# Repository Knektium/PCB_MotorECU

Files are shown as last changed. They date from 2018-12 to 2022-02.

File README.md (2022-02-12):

Wolley Motor ECU
================

This is the KiCad project for the PCB that is used as ECU for the Wolley Wheel
and Fan modules.

It's a circular PCB that a brushed DC motor can be directly mounted on to be
controlled by the driver and MCU onboard through CAN.

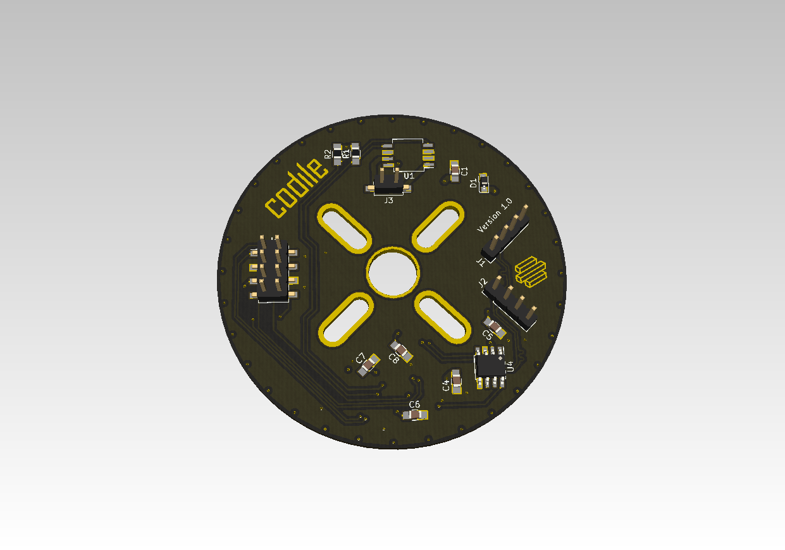
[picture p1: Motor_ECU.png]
PCB rendered in KiCad


Specifications
--------------

| Name | Value |
| --- | --- |
| PCB layers | 2 |
| PCB diameter | 61 mm |
| Max motor diameter | 28 mm |
| Motor center hole diameter | 10 mm |
| Motor voltage | 6 - 36 V |
| Max motor current | 6 A |
| Control Interface | CAN |

Key Components
--------------

| Component | Part | Details |
| --- | ---- | --- |
| MCU | Infineon XMC1404_F064X200A | ARM Cortex-M0, 32-bit, 48 MHz, 200 kB flash |
| Motor driver | Infineon IFX9201SG | 6 A and 36 V H-bridge with SPI diagnostics |
| CAN transceiver | Infineon TLE7251VSJ | |
| Speed sensor | Infineon TLE4964-4M | High precision unipolar hall effect switch |
| Temperature sensor | TI LM35DM | Precision centigrade temperature sensor |

Motor Alternatives
------------------

 - Mabuchi RS-385PV-2465
 - Mabuchi RS-365

Release Notes
-------------

Version 1.4:
 - Replaced the 4-pin connector with the new 5-pin connector.
 - Removed the battery power connector.

Version 1.3:
 - Moved the connectors closer to the middle to allow for more space and
   therefore better mounting.
 - Added a key hole to prevent the PCB from spinning when used as the
   CentrifugalFan ECU.
 - Joined the mount holes with the motor hole.
 - Smaller silk screen improvements.

Version 1.2 (same as CentrifugalFanECU v1.0):
 - Added a dedicated connector for the motor power.
 - Added a temperature sensor.
 - Added a status LED.
 - Removed two of the mount holes.
 - Made the motor hole bigger to fit a Mabuchi RS-380.

Version 1.1:
 - Replaced the motor driver with a better one that can handle up to 36 V.
 - Other improvements.

Licence
-------

Licenced under the CERN Open Hardware Licence v1.2.

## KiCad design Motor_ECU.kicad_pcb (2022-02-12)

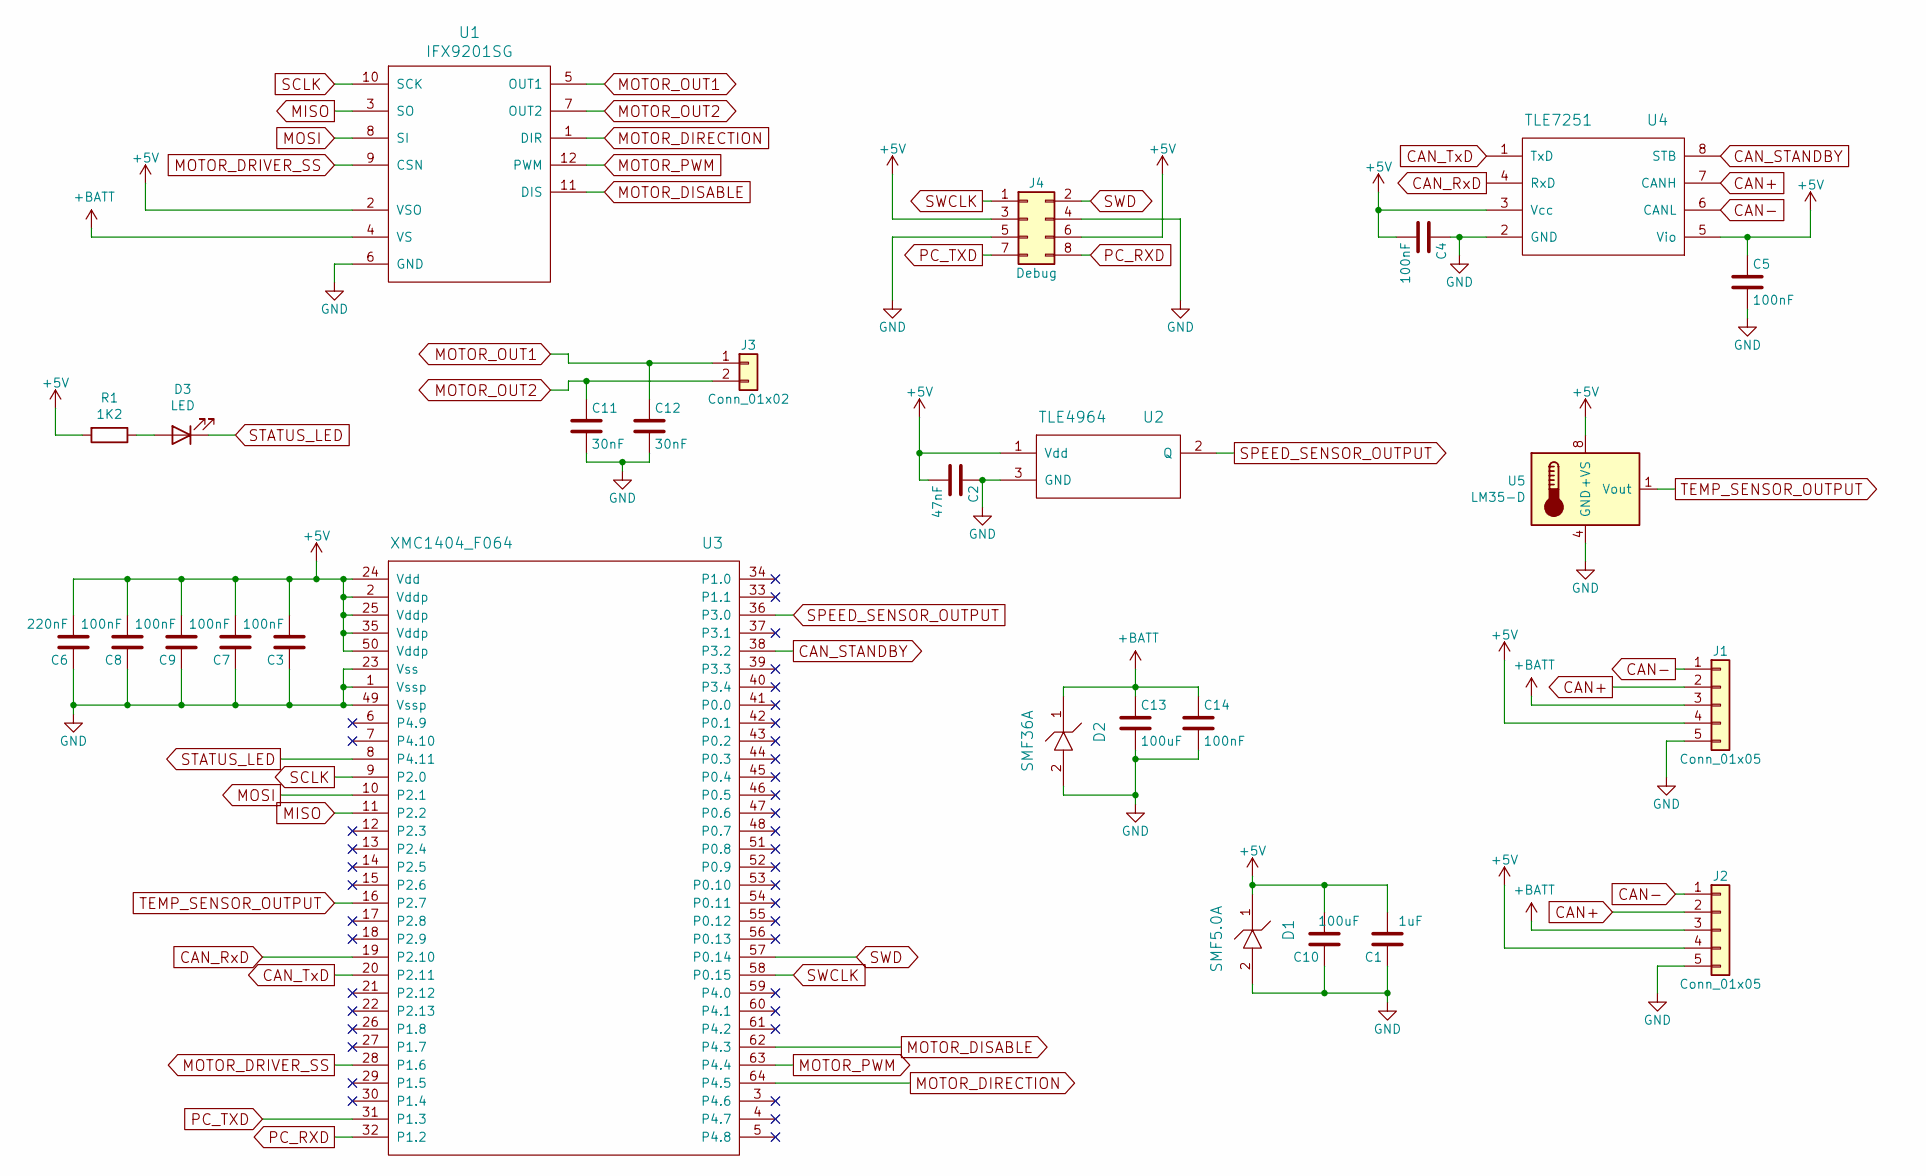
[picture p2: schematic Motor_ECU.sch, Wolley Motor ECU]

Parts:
C1: 1uF; C_0805_HandSoldering
C2: 47nF; C_0805_HandSoldering
C3, C4, C5, C7, C8, C9, C14: 100nF; C_0805_HandSoldering
C6: 220nF; C_0805_HandSoldering
C10, C13: 100uF; C_0805_HandSoldering
C11, C12: 30nF; C_0805_HandSoldering
D1: SMF5.0A; D_SOD-123F
D2: SMF36A; D_SOD-123F
D3: LED; C_0805_HandSoldering
J1, J2: Conn_01x05; PinHeader_1x05_P2.54mm_Vertical
J3: Conn_01x02; PinHeader_1x02_P2.54mm_Vertical
J4: Debug; Pin_Header_Straight_2x04_Pitch2.54mm_SMD
R1: 1K2; C_0805_HandSoldering
U1: IFX9201SG; SOIC-12_HeatSlugs
U2: TLE4964; TSOT-23_HandSoldering
U3: XMC1404_F064; TQFP-64_10x10mm_Pitch0.5mm_Handsoldering
U4: TLE7251; SOIC-8_3.9x4.9mm_Pitch1.27mm
U5: LM35-D; SOIC-8_3.9x4.9mm_P1.27mm

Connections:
+5V: C1.2, C2.2, C3.2, C4.2, C5.1, C6.2, C7.2, C8.2, C9.2, C10.2, D1.1, J1.4, J2.4, J4.3, J4.6, R1.2, U1.2 (VSO), U2.1 (Vdd), U3.2 (Vddp), U3.24 (Vdd), U3.25 (Vddp), U3.35 (Vddp), U3.50 (Vddp), U4.3 (Vcc), U4.5 (Vio), U5.8 (+VS)
+BATT: C13.1, C14.1, D2.1, J1.3, J2.3, U1.4 (VS)
CAN+: J1.2, J2.2, U4.7 (CANH)
CAN-: J1.1, J2.1, U4.6 (CANL)
CAN_RxD: U3.19 (P2.10), U4.4 (RxD)
CAN_STANDBY: U3.38 (P3.2), U4.8 (STB)
CAN_TxD: U3.20 (P2.11), U4.1 (TxD)
GND: C1.1, C2.1, C3.1, C4.1, C5.2, C6.1, C7.1, C8.1, C9.1, C10.1, C11.2, C12.2, C13.2, C14.2, D1.2, D2.2, J1.5, J2.5, J4.4, J4.5, U1.6 (GND), U2.3 (GND), U3.1 (Vssp), U3.23 (Vss), U3.49 (Vssp), U4.2 (GND), U5.4 (GND)
MISO: U1.3 (SO), U3.11 (P2.2)
MOSI: U1.8 (SI), U3.10 (P2.1)
MOTOR_DIRECTION: U1.1 (DIR), U3.64 (P4.5)
MOTOR_DISABLE: U1.11 (DIS), U3.62 (P4.3)
MOTOR_DRIVER_SS: U1.9 (CSN), U3.28 (P1.6)
MOTOR_OUT1: C12.1, J3.1, U1.5 (OUT1)
MOTOR_OUT2: C11.1, J3.2, U1.7 (OUT2)
MOTOR_PWM: U1.12 (PWM), U3.63 (P4.4)
unnamed: D3.2 (A), R1.1
PC_RXD: J4.8, U3.32 (P1.2)
PC_TXD: J4.7, U3.31 (P1.3)
SCLK: U1.10 (SCK), U3.9 (P2.0)
SPEED_SENSOR_OUTPUT: U2.2 (Q), U3.36 (P3.0)
STATUS_LED: D3.1 (K), U3.8 (P4.11)
SWCLK: J4.1, U3.58 (P0.15)
SWD: J4.2, U3.57 (P0.14)
TEMP_SENSOR_OUTPUT: U3.16 (P2.7), U5.1 (Vout)

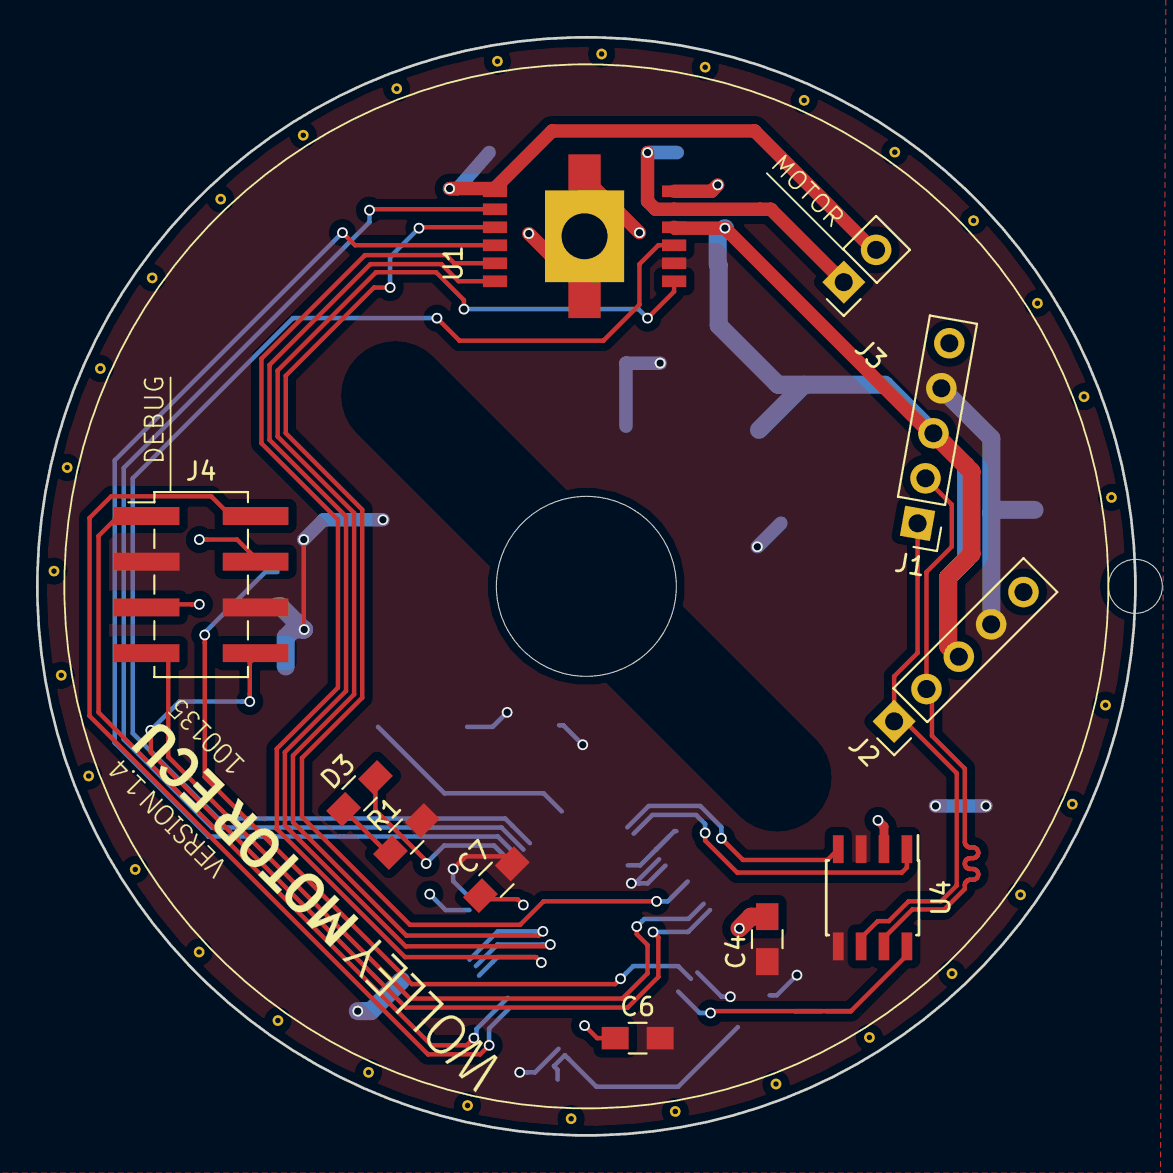
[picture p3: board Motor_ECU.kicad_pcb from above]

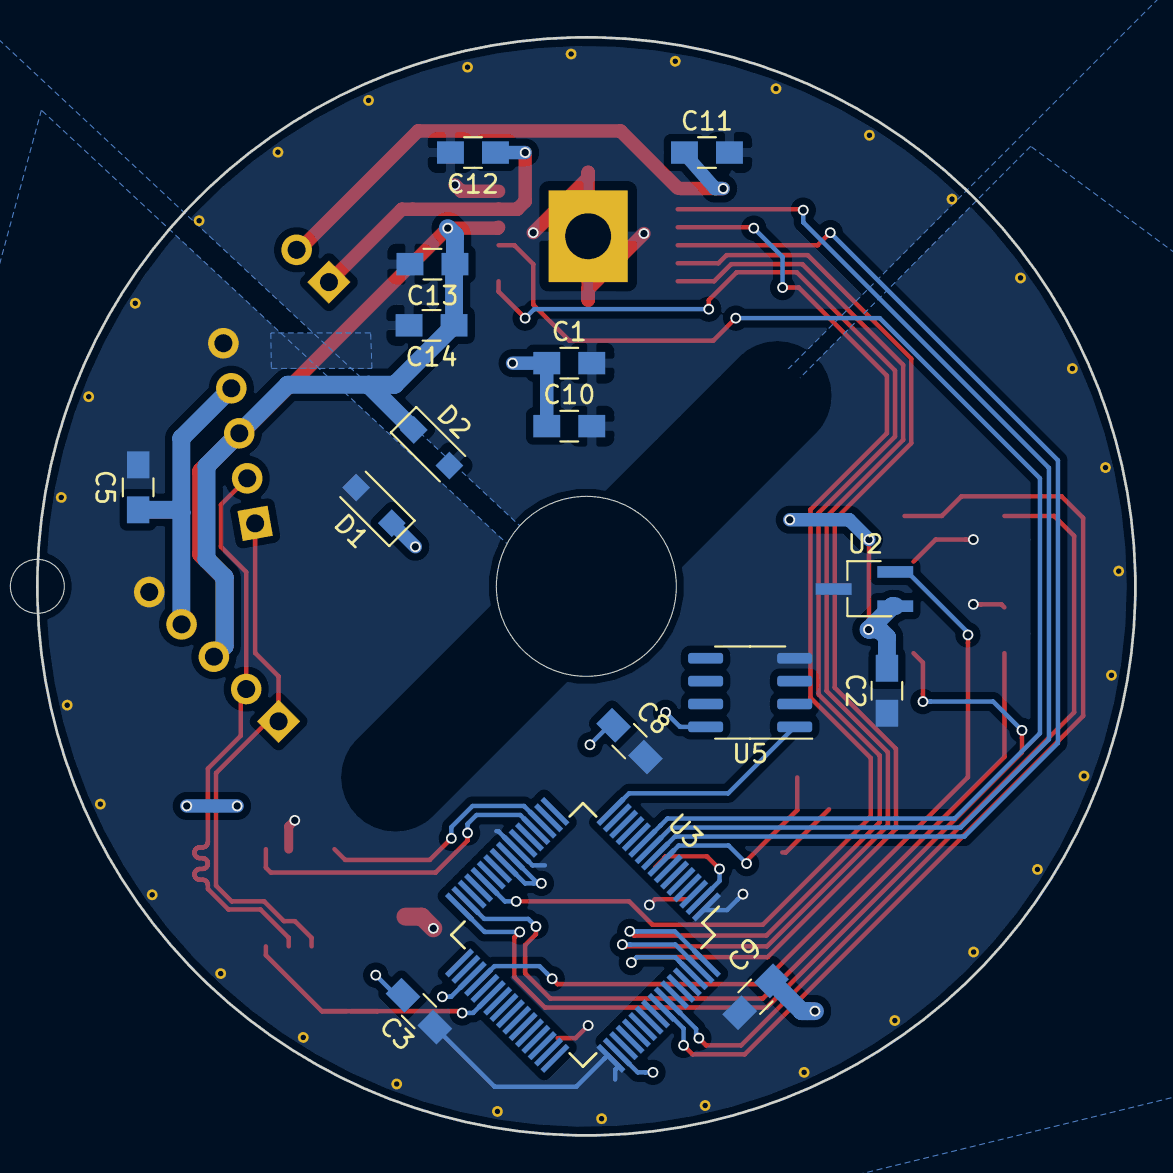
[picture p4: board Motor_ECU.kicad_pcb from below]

Board: 2 copper layers, 61.0 x 61.0 mm, 30 parts (16 on the bottom side), 25 nets.

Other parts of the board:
M**: Motor_Mount_Hole; Mount_Hole_M3x6.5
M**#2: Motor_Mount_Hole; Mount_Hole_M3x6.5
M**#3: Motor_Center_Hole

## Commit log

2018-12-10 Add KiCad files
    [Wheel_ECU.kicad_pcb, Wheel_ECU.sch]
2018-12-10 Moved mount hole footprint files to root dir along with other footprints
2018-12-12 Add Wolley Interconnect logo footprint to local library
    [Wheel_ECU.kicad_pcb]
2020-12-07 Replace the motor driver and other improvements
    [Wheel_ECU.kicad_pcb, Wheel_ECU.sch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]
2021-07-21 Copy the changes from the CentrifugalFan module
    [Wheel_ECU.kicad_pcb, Wheel_ECU.sch]
2021-07-21 Rename the schematic
    [Wheel_ECU.sch]
2021-07-21 Change the version text on the PCB
    [Wheel_ECU.kicad_pcb]
2021-08-01 Move connectors closer to middle
    [Wheel_ECU.kicad_pcb]
2021-08-01 Smaller clean up
    [Wheel_ECU.kicad_pcb]
2021-08-01 Add key hole
    [Wheel_ECU.kicad_pcb]
2021-08-01 Join the mount holes with the motor hole
    [Wheel_ECU.kicad_pcb]
2021-08-01 Fix silk screen and texts and smaller improvements
    [Wheel_ECU.kicad_pcb]
2021-08-01 Update gerber files for v1.3
    [PCB_StandardWheelECU.drills_pth.xln, PCB_StandardWheelECU.holes_npth.xln, Wheel_ECU-NPTH-drl_map.gbr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]
2021-08-02 Relocate the second connector a bit and add mor space between the labels
    [Wheel_ECU.kicad_pcb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]
2021-08-05 Rename the PCB to Motor ECU since it is shared between more than one module
    [Wheel_ECU.kicad_pcb, Wheel_ECU.sch]
2021-08-05 Rename the files to reflect the project name
    [Motor_ECU.kicad_pcb, Motor_ECU.sch]
2021-08-05 Clean up in the symbol libs
    [Motor_ECU.sch]
2022-02-12 Replace the 4-pin connectors with the new 5-pin connector
    [Motor_ECU.kicad_pcb, Motor_ECU.sch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]
